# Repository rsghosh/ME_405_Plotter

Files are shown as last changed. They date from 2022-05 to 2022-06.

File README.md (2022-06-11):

# ME 405 Pen Plotter

Ryan Ghosh and Ryan Flaherty (mecha18)

ME 405-03

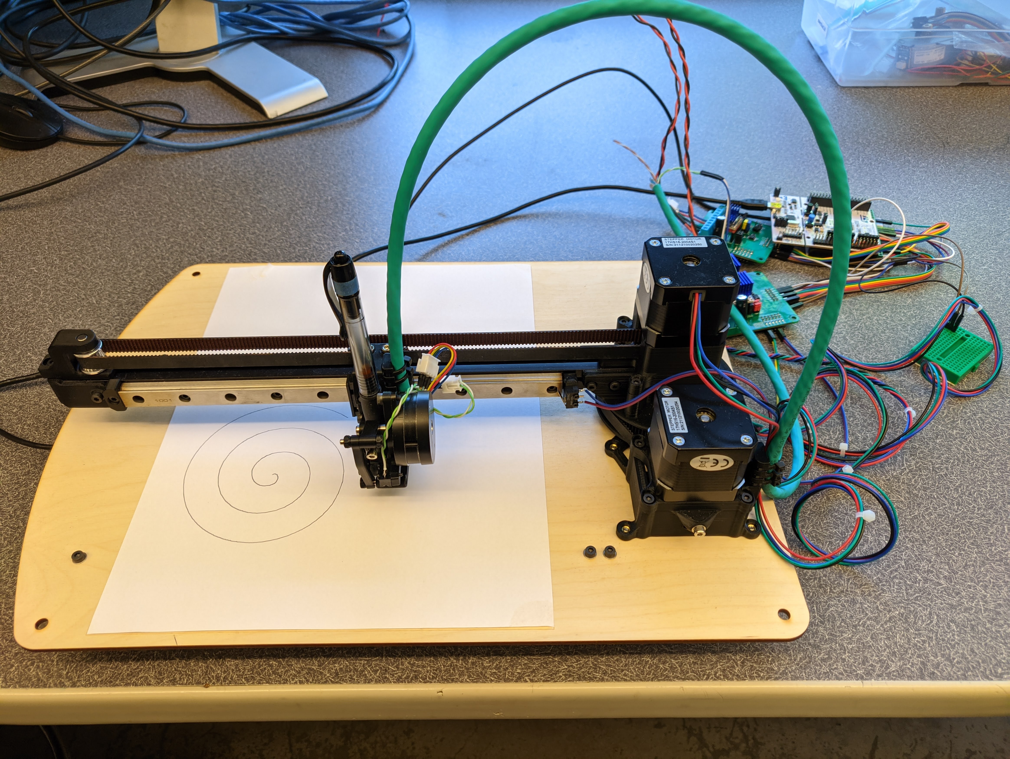
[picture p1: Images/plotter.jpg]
Pen Plotter


## Introduction

For our ME 405 term project, we designed, built, and programmed a polar pen plotter.
A Nucleo board on the plotter reads an hpgl file, converts the commands to motor positions, and controls the stepper drivers to make the plotter draw. Meanwhile, a PC receives the commands over UART to draw the same shapes on the screen in sync with the plotter.

The following videos show the plotter in action:
- [Drawing a pentagon, hexagon, and line](https://photos.app.goo.gl/KpNNWDwEAwex2bkJ8)
- [Drawing a spiral](https://photos.app.goo.gl/GEohXohUGA1frtkg9)

## Python Code

[Documentation](https://rsghosh.github.io/ME_405_Plotter/)

[Source code](https://github.com/rsghosh/ME_405_Plotter/tree/master/Python_Code)

## CAD Files

SolidWorks files for the pen plotter can be found [here.](https://github.com/rsghosh/ME_405_Plotter/tree/master/CAD)

## STL and DXF Files

All custom parts for the plotter are either 3D-printed or laser-cut.

### 3D-Printed Files

All stl files can be found in the [STLs folder.](https://github.com/rsghosh/ME_405_Plotter/tree/master/STLs)

In each filename, `_x#` indicates the quantity required, and `_rev#` indicates the revision number.

### Laser-Cut Files

The base for the plotter should be laser-cut from 3mm or 0.125" thick material. The dxf file can be found in the [DXFs folder.](https://github.com/rsghosh/ME_405_Plotter/tree/master/DXFs)

## Bill of Materials

The following table contains all the parts you need for the pen plotter that are not either 3D-printed or laser-cut:

| Item # | Description | Quantity | Source |
| --- | --- | --- | --- |
| 1 | 1515 Extrusion (300mm long) | 3 | [Amazon](https://www.amazon.com/MakerBeam-XL-Anodized-300x15x15mm-Pieces/dp/B06XJ5G5QY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)  |
| 2 | MGN12C Rail (240mm long) | 1 | [RobotDigg](https://www.robotdigg.com/product/766/Quality-440C-SUS-MGN12-linear-rail-with-carriage) |
| 3 | NEMA17 Stepper Motor | 2 | [Printed Solid](https://www.printedsolid.com/collections/motors/products/ldo-nema-17-motor-cooler-ldo-42sth40-1004asr)  |
| 4 | 2GT 20T Toothed Idler (for 9mm belt)  | 1 | [Printed Solid](https://www.printedsolid.com/products/gates-powergrip-2gt-toothed-idler-5mm-id?variant=21236971274325) |
| 5 | 2GT 20T Pulley (for 9mm belt) | 2 | [Printed Solid](https://www.printedsolid.com/products/gates-powergrip-2gt-pulley?variant=21236966948949)  |
| 7 | 6201 Bearing | 2 | [AliExpress](https://www.aliexpress.com/item/32861605867.html) |
| 8 | 5x25mm Shaft | 1 | [AliExpress](https://www.aliexpress.com/item/2255800484105446.html?gatewayAdapt=4itemAdapt) |
| 9 | 3x20mm Shaft | 3 | [Misumi](https://us.misumi-ec.com/vona2/detail/110300086920/?HissuCode=NSFR3-20)  |
| 10 | 5x7x0.5mm Shim | 2 | [AliExpress](http://s.click.aliexpress.com/e/_sq74Gk) |
| 11 | Omron D2F-L Microswitch | 3 | [Digikey](https://www.digikey.com/en/products/detail/omron-electronics-inc-emc-div/D2F-01L/83264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) |
| 12 | M3 Square Nut (DIN 562) | 36 | [McMaster-Carr](https://www.mcmaster.com/97259A101/)  |
| 13 | M3 x 8mm Socket Head Cap Screw | 59 | [McMaster-Carr](https://www.mcmaster.com/91290a113) |
| 14 | M3 x 10mm Socket Head Cap Screw | 5 | [McMaster-Carr](https://www.mcmaster.com/91290A115/)  |
| 15 | M3 x 12mm Socket Head Cap Screw | 12 | [McMaster-Carr](https://www.mcmaster.com/91290A117) |
| 16 | M3 x 20mm Socket Head Cap Screw | 2 | [McMaster-Carr](https://www.mcmaster.com/91290A123/)  |
| 17 | M3 Heat-Set Insert (M3 x D5.0 x L4.0) | 27 | [AliExpress](http://s.click.aliexpress.com/e/oMUr6YsC) |
| 18 | M3 Washer (narrow) | 8 | [McMaster-Carr](https://www.mcmaster.com/91166A210/)  |
| 19 | M3 Washer (large) | 4 | [McMaster-Carr](https://www.mcmaster.com/91100A120/)  |
| 20 | 36mm Round NEMA14 Stepper | 1 | [Printed Solid](https://www.printedsolid.com/products/ldo-nema14-36mm-round-pancake-motor-ldo-36sth17-1004ah)
| 21 | M5 x 45mm Socket Head Cap Screw | 1 | [McMaster-Carr](https://www.mcmaster.com/91290A260/)  |
| 22 | M2 x 12mm Pan Head Self Tapping Screw | 6 | [AliExpress](http://s.click.aliexpress.com/e/ojcLGreY) |
| 23 | M5 Locknut | 1 | [McMaster-Carr](https://www.mcmaster.com/90576A104/)  |
| 24 | Unthreaded Bumper | 4 | [McMaster-Carr](https://www.mcmaster.com/9540K921/) |
| 25 | Nucleo-L476RG | 1 | [Digikey](https://www.digikey.com/en/products/detail/stmicroelectronics/NUCLEO-L476RG/5347711) |
| 26 | TMC2208 Stepstick | 3 | [Amazon](https://www.amazon.com/Printer-TMC2208-Screwdriver-Controller-Ramps1-4/dp/B082LSQWZF) |
| 27 | Stepper Driver Board | 2 | |

## Wiring

### Stepper Driver Board #1
| Signal | Nucleo Pin | Color |
| --- | --- | --- |
| EN1 | C2 | red |
| EN2 | C3 | green |
| GND | GND | black |
| 3V3 | 3V3 | gray  |
| CLK | PB6 | brown |
| CS1 | PB8 | yellow|
| CS2 | PB9 | orange|
| SCK | PB13 (SPI2_SCLK)  | blue  |
| MOSI | PB15 (SPI2_MOSI)  | white |
| MISO | PB14 (SPI2_MISO)  | purple|

### Stepper Driver Board #2
| Signal | Nucleo Pin | Color |
| --- | --- | --- |
| EN1 | C6 | blue  |
| GND | GND | green |
| 3V3 | 3V3 | yellow|
| CLK | PB6 | brown |
| CS1 | C7 | orange|
| CS2 | 3V3 | white |
| SCK | PB13 (SPI2_SCLK)  | blue  |
| MOSI | PB15 (SPI2_MOSI)  | white |
| MISO | PB14 (SPI2_MISO)  | purple|

### Limit Switch Wiring

The wires should be soldered to the outermost legs on the limit switches so that they are normally closed.

| Endstop | Stepper Board # | Pin |
| --- | --- | --- |
| theta | 1 | REFL1 |
| radius | 1 | REFL2 |
| pen up/down | 2 | REFL1 |

### Stepper Driver Board Jumpers

To set the TMC2208 drivers to use 8 microsteps, jumpers should be placed on the JP6 and JP7 headers to short MS1 and MS2 to GND.

### Setting VREF

To calculate the VREF values to set on the TMC2208 drivers, the desired RMS current should be multiplied by 1.41 ohm.

The following table shows the VREF values we used:

| Motor | Target RMS Current (A) | VREF (V)  |
| --- | --- | --- |
| theta | 1.13 | 1.59 |
| radius | 1.13 | 1.59 |
| pen up/down | 0.35 | 0.49 |

### Wiring Example

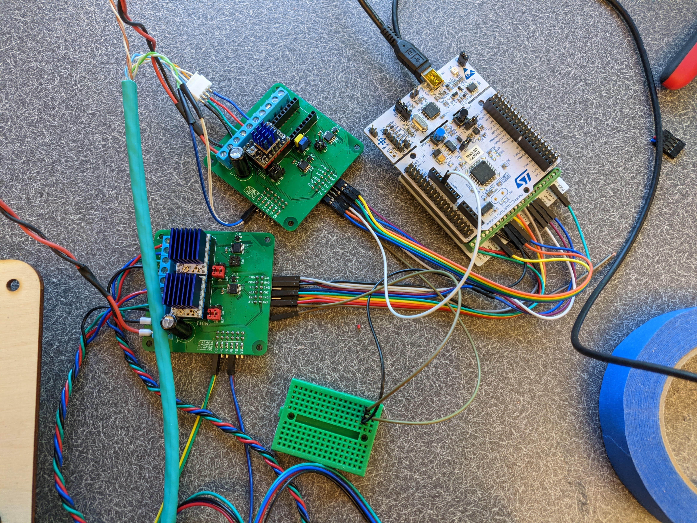
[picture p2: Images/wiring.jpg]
Wiring Example


## Task Diagram

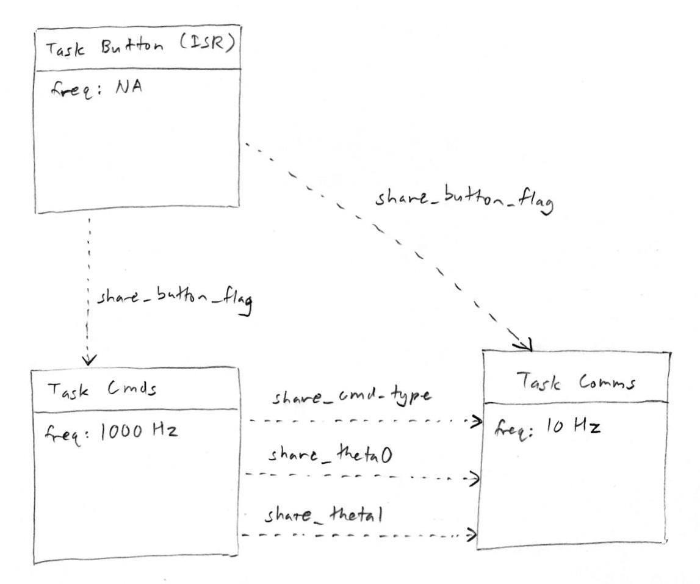
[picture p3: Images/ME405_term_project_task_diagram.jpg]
Task Diagram


## Kinematics

Since our pen plotter uses one motor for controlling the angle of the arm and another to control the radius, we had to use inverse kinematics to determine the motor angles needed to get the pen to the target x and y coordinates. We used the Newtom-Raphson algorithm to find the required motor angles to reach the target position. The following images show the steps we took to find the matrices and equations we would use in the algorithm:

1. Simplified schematic of the robot with links and pivots
2. Forward kinematics: determine `x = f(theta)`, where theta is the motor angles and x is the pen position
3. Find the Jacobian matrix for the system
4. Differentiate `x = f(theta)` with respect to time to find velocity
5. Find g(theta), where `g(theta) = x - f(theta)` and x is a constant target position. Then differentiate g with respect to theta.

We then used these equations in the NewtonRaphson function in [tasks.py](https://github.com/rsghosh/ME_405_Plotter/blob/master/Python_Code/tasks.py) to convert pen positions read from the hpgl file into motor angles.

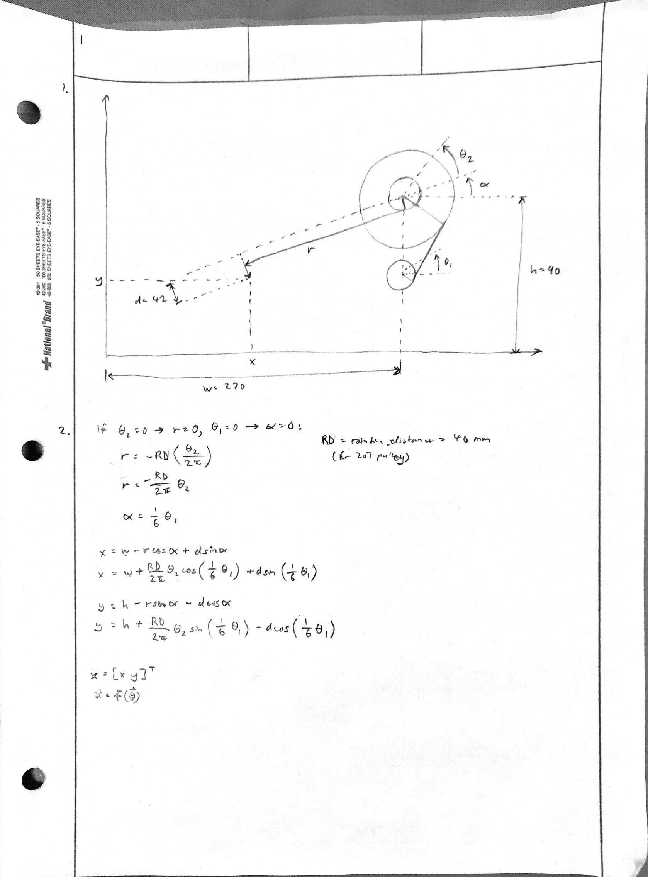
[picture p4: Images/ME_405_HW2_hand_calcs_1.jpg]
Kinematics steps 1-2


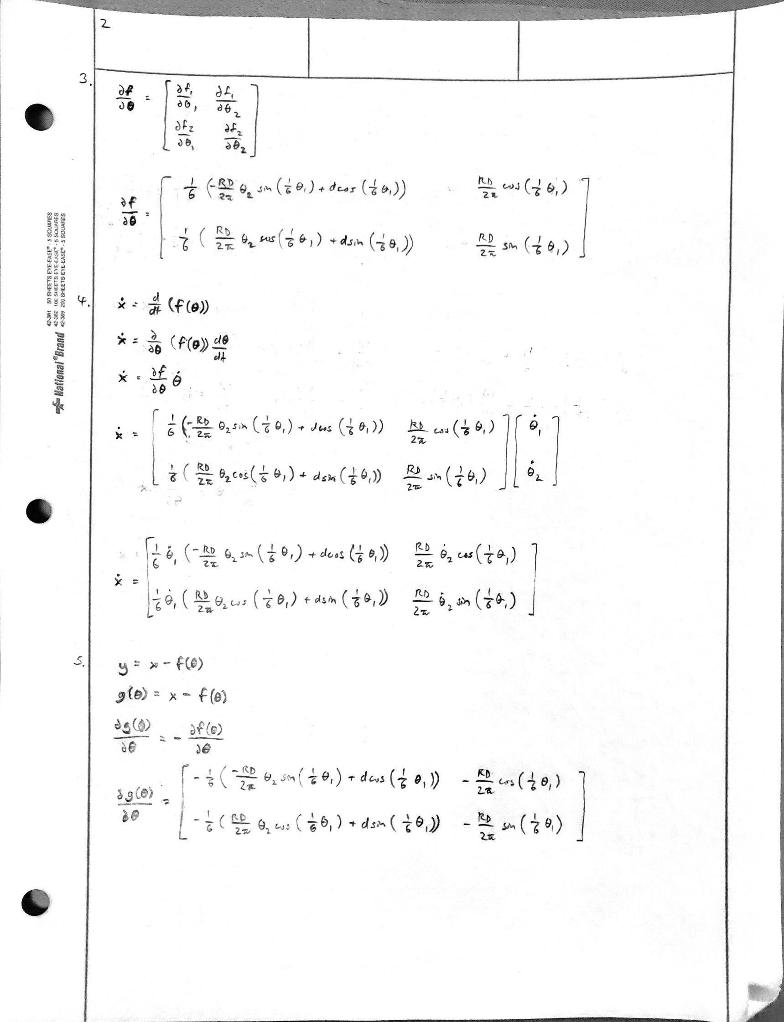
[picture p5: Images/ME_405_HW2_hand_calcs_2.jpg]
Kinematics steps 3-5


## Program Flow

[tasks.py](https://github.com/rsghosh/ME_405_Plotter/blob/master/Python_Code/tasks.py) contains the main function that runs on the Nucleo. The program proceeds in the following steps:
- Read an hpgl file and split it into separate commands
- convert target positions into millimeters
- Interpolate between points so that the minimum distnance between any two points is less than or equal to `MAX_MM_DIST` (which we set to 0.5mm)
- Use Newton-Raphson to convert the positions to theta angles for the motors
- Convert theta angles to numbers in units of microsteps that can be sent to the TMC4210s as the X_TARGET
- Configure the TMC4210 and TMC2208 chips
- Home all three steppers
- Wait for a button press
- Start the two tasks:
  - task_cmds: reads through the commands and sends them to the TMC4210s
  - task_comms: sends the current command to the PC via UART to be plotted on the screen
- Disable the motors once the end of the command list has been reached

More details on the individual functions can be found in the [documentation for the python files.](https://rsghosh.github.io/ME_405_Plotter/)

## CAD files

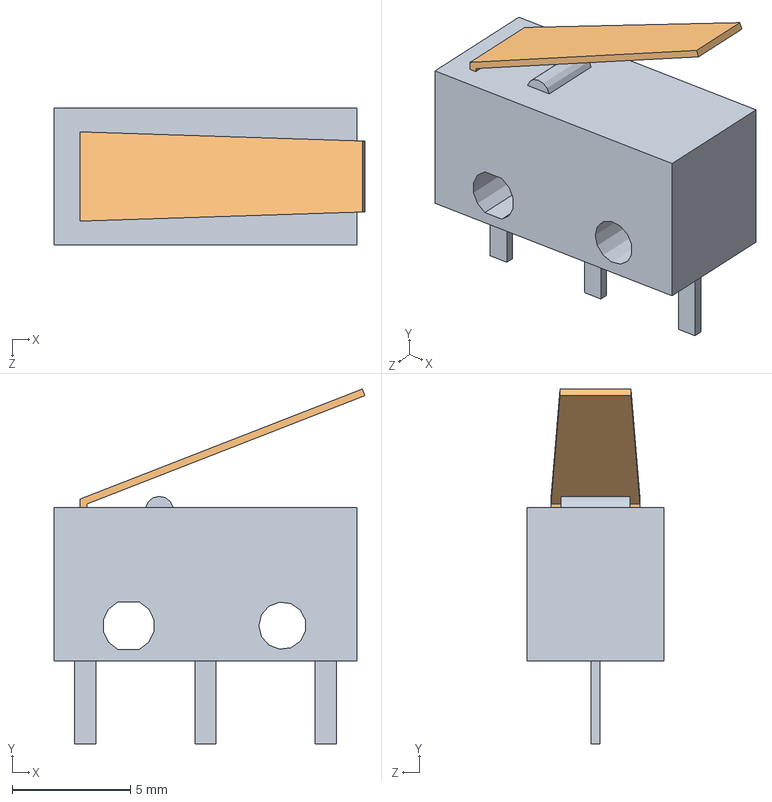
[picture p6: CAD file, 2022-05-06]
CAD/hardware/D2F_01L_Solidworks/D2F_01L.SLDASM
13.1 x 15.0 x 5.80 mm
D2F_01L_BASE
D2F_01L_ACTUATOR

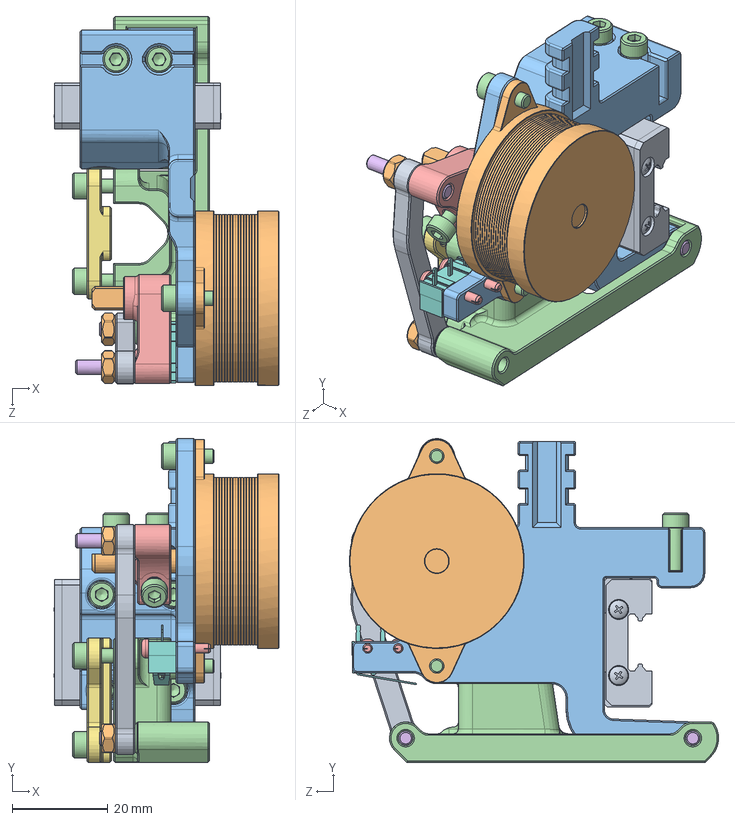
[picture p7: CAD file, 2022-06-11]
CAD/Toolhead.SLDASM
46.9 x 67.7 x 77.1 mm
MGN12C, LINEAR GUIDE BLOCK
LDO-36STH20-1004AH Mockup
Carriage^Toolhead
Pen Arm^Toolhead
Motor Arm^Toolhead
Shaft 3x20 x 3
Pen Clamp^Toolhead
49 MICRO D2F-L
Link^Toolhead
3mm Shaft Retainer x 2
square nut thin grade b_din
socket head cap screw_am x 13
pan head tapping screw_am x 2
94180A331_HEAT-SET INSERTS FOR PLASTICS x 4

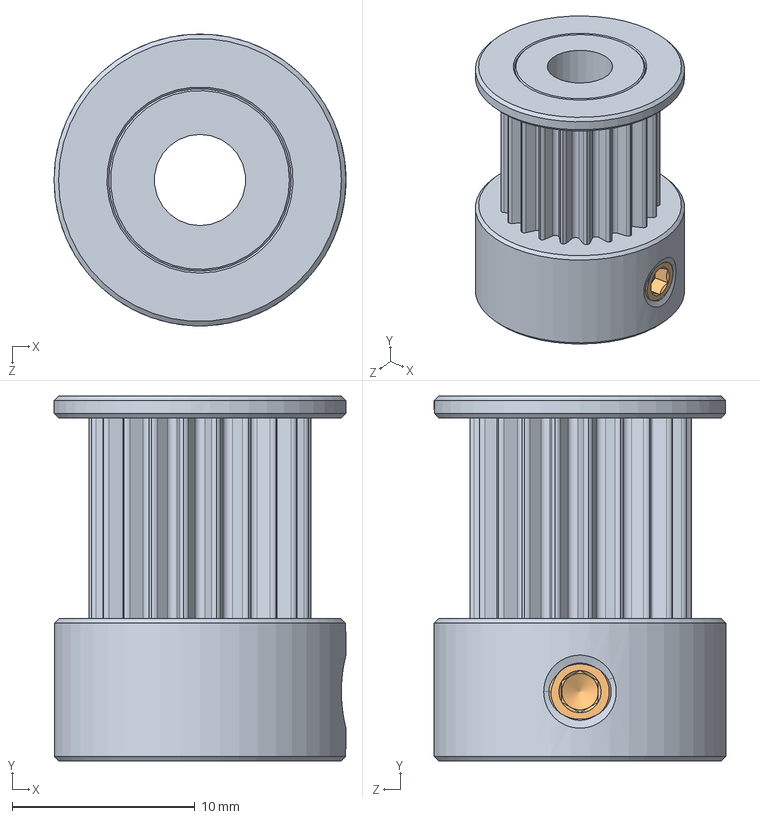
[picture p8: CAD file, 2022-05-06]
CAD/hardware/Pulley 9mm 20T 2GT/Pulley, 9mm GT2.SLDASM
16.0 x 20.0 x 16.0 mm
Pulley, 9mm GT2
91390A110

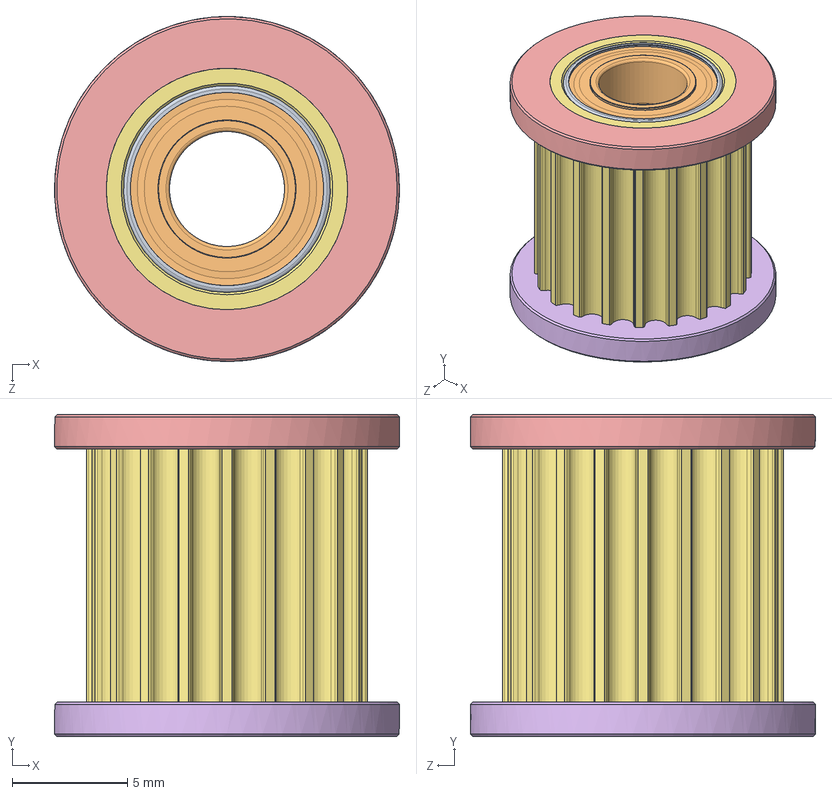
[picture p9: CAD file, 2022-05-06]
CAD/hardware/20T Toothed Idler/Pulley, 2GT 20T Toothed Idler (11mm wide).SLDASM
15.0 x 14.0 x 15.0 mm
Pulley, 2GT 20T Toothed Idler (11mm wide)_4
Pulley, 2GT 20T Toothed Idler (11mm wide)_14
Pulley, 2GT 20T Toothed Idler (11mm wide)_8
Pulley, 2GT 20T Toothed Idler (11mm wide)_19
Pulley, 2GT 20T Toothed Idler (11mm wide)_17
Pulley, 2GT 20T Toothed Idler (11mm wide)_16
Pulley, 2GT 20T Toothed Idler (11mm wide)_13
Pulley, 2GT 20T Toothed Idler (11mm wide)_22
Pulley, 2GT 20T Toothed Idler (11mm wide)_18
Pulley, 2GT 20T Toothed Idler (11mm wide)
Pulley, 2GT 20T Toothed Idler (11mm wide)_9
Pulley, 2GT 20T Toothed Idler (11mm wide)_2
Pulley, 2GT 20T Toothed Idler (11mm wide)_10
Pulley, 2GT 20T Toothed Idler (11mm wide)_23
Pulley, 2GT 20T Toothed Idler (11mm wide)_20
Pulley, 2GT 20T Toothed Idler (11mm wide)_3
Pulley, 2GT 20T Toothed Idler (11mm wide)_5
Pulley, 2GT 20T Toothed Idler (11mm wide)_11
Pulley, 2GT 20T Toothed Idler (11mm wide)_21
Pulley, 2GT 20T Toothed Idler (11mm wide)_12
Pulley, 2GT 20T Toothed Idler (11mm wide)_6
Pulley, 2GT 20T Toothed Idler (11mm wide)_15
Pulley, 2GT 20T Toothed Idler (11mm wide)_7

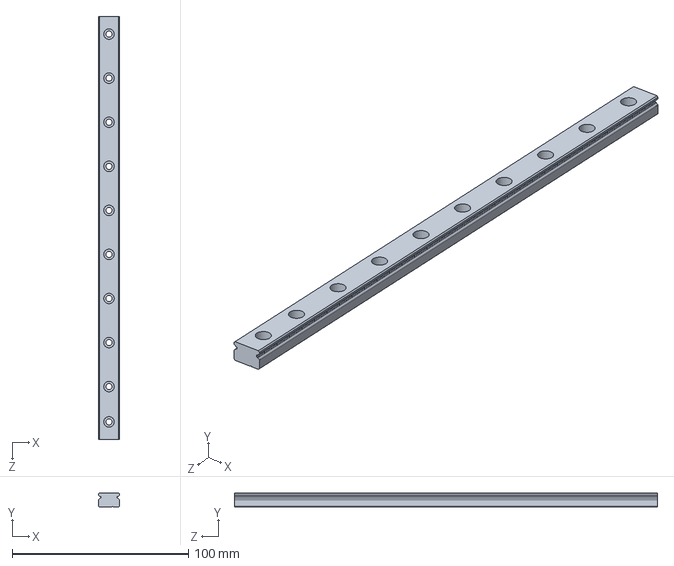
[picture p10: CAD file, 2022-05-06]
CAD/hardware/MGN12C Linear Guide/MGN12 LINEAR GUIDE RAIL, CONFIGURABLE.SLDPRT
12.0 x 8.00 x 240.0 mm

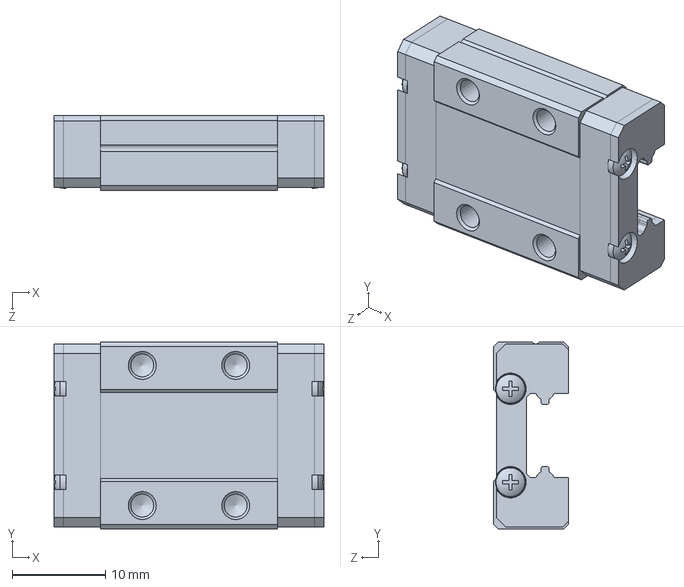
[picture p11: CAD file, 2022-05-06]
CAD/hardware/MGN9CZFC [Hiwin].SLDPRT
28.9 x 20.0 x 8.00 mm

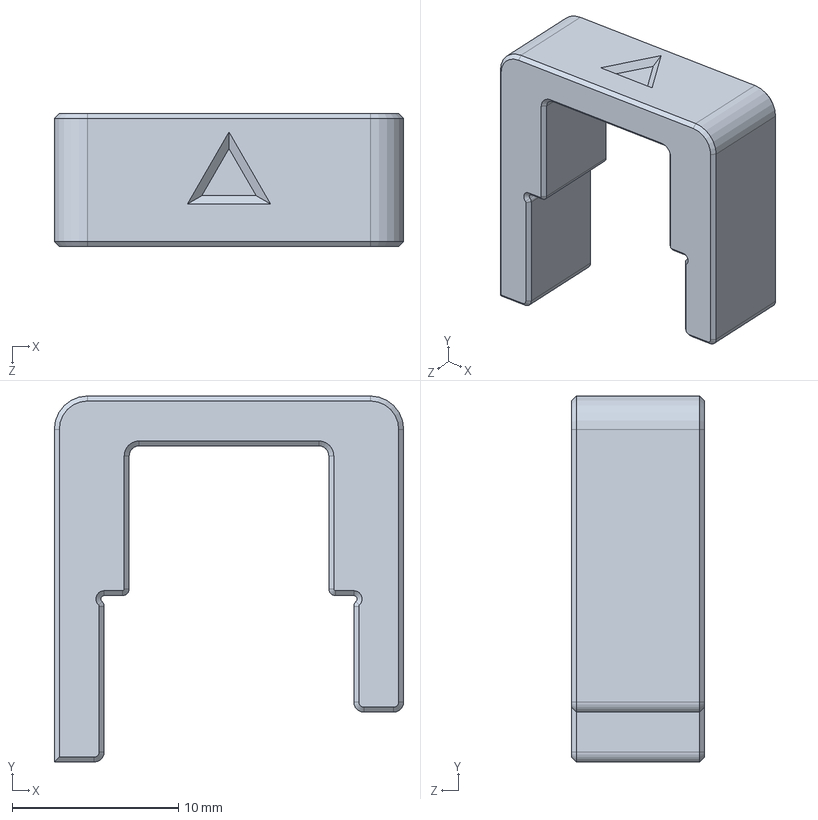
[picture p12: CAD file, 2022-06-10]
CAD/tools/MGN12 1515 Rail Installation Guide.SLDPRT
21.0 x 22.0 x 8.00 mm

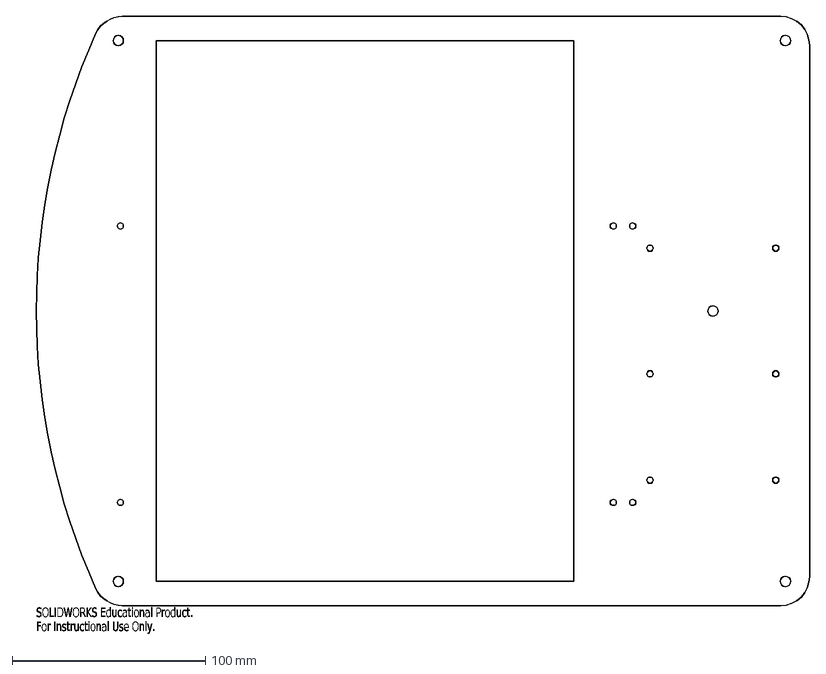
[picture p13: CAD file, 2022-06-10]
DXFs/BASE-PLATE-2.DXF
SOLIDWORKS Educational Product.
For Instructional Use Only.

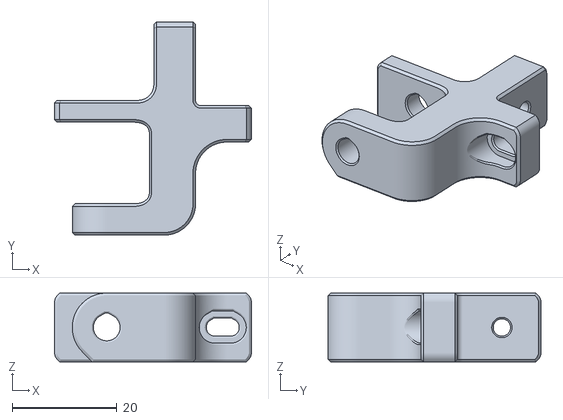
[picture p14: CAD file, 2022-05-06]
STLs/Arm/idler_tensioner_moving_x1_rev1.STL
37.7 x 40.8 x 13.2

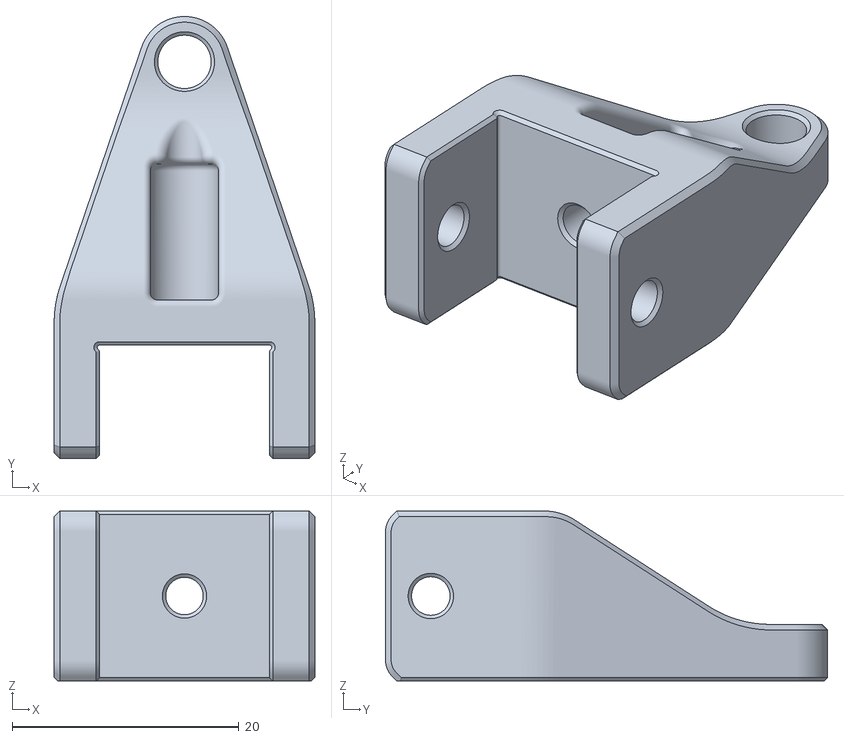
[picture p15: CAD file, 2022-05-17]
STLs/Base/plate_mount_x2_rev1.STL
23.0 x 39.0 x 15.0

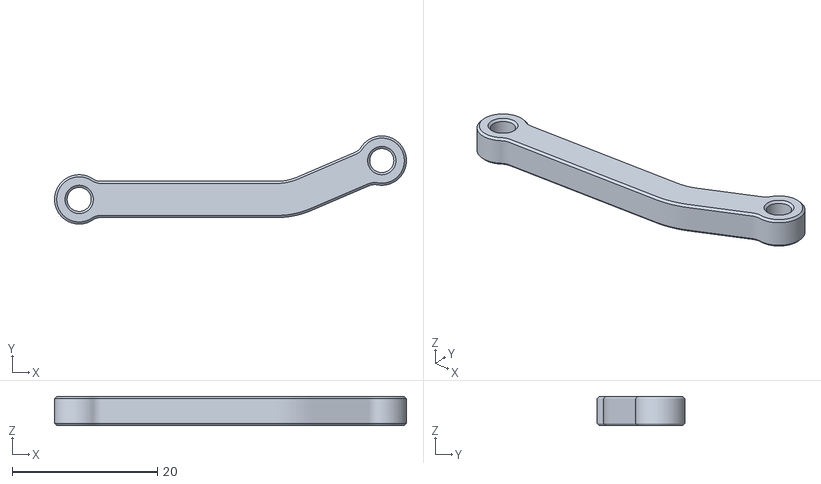
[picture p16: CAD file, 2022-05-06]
STLs/Toolhead/link_x1_rev1.STL
48.4 x 12.1 x 4.00

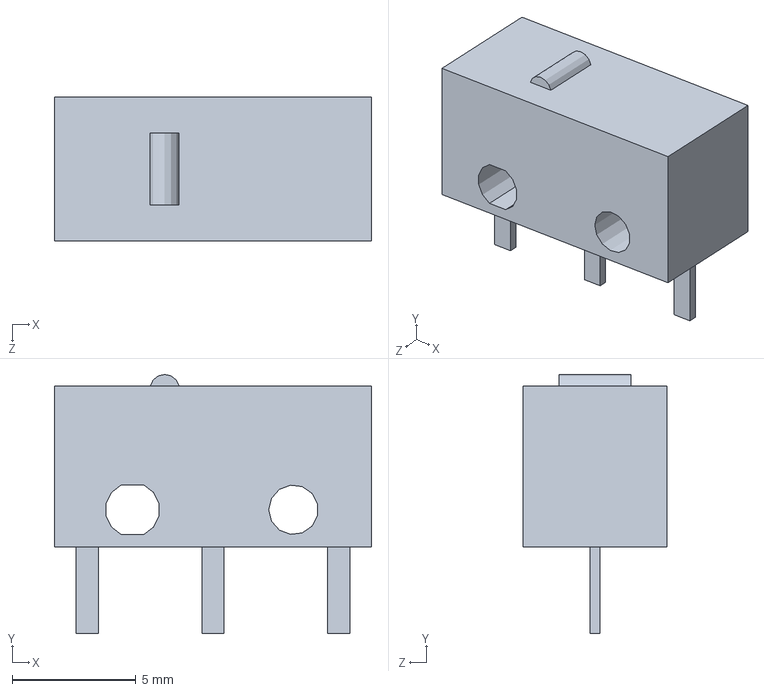
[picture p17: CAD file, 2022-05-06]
CAD/hardware/D2F_01L_Solidworks/D2F_01L_BASE.SLDPRT
12.8 x 10.5 x 5.80 mm

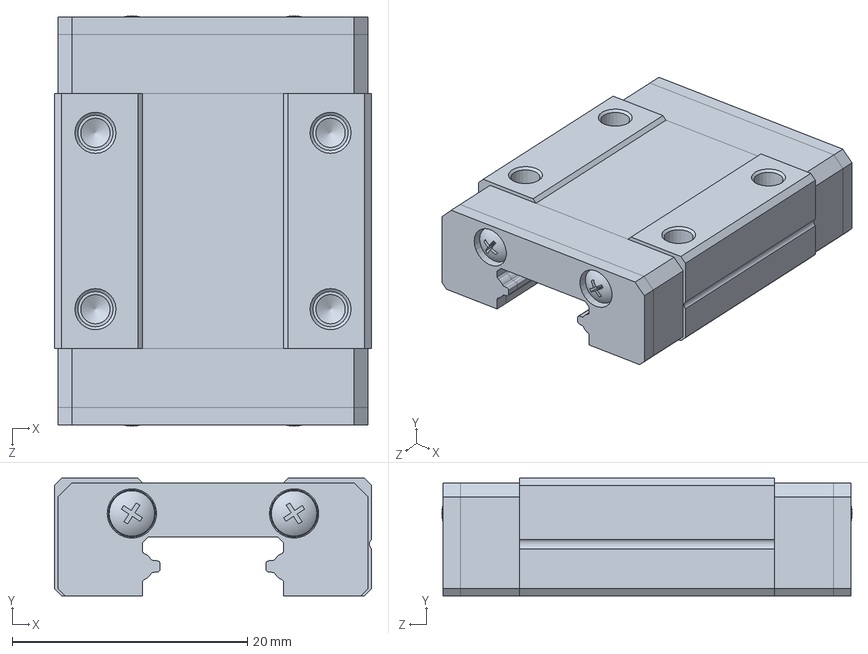
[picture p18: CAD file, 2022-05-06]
CAD/hardware/MGN12C Linear Guide/MGN12C, LINEAR GUIDE BLOCK.SLDPRT
27.0 x 10.0 x 34.9 mm

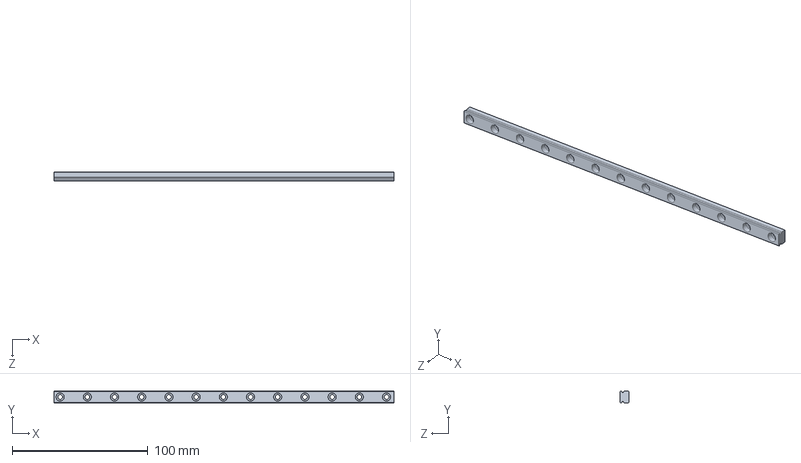
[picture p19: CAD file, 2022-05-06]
CAD/hardware/MGN9 Rail 250mm.SLDPRT
250.0 x 9.00 x 6.50 mm

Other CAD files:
CAD/hardware/20T Toothed Idler/Pulley, 2GT 20T Toothed Idler (11mm wide)_22.SLDPRT
CAD/hardware/20T Toothed Idler/Pulley, 2GT 20T Toothed Idler (11mm wide)_5.SLDPRT
CAD/MDF Base Plate (Laser Cut).SLDPRT
STLs/Arm/radius_limit_switch_mount_x1_rev1.STL
CAD/3mm Shaft Retainer.SLDPRT
CAD/Clipboard Clamp.SLDPRT
CAD/Printed M5 Washer.SLDPRT
CAD/hardware/20T Toothed Idler/Pulley, 2GT 20T Toothed Idler (11mm wide).SLDPRT
CAD/hardware/20T Toothed Idler/Pulley, 2GT 20T Toothed Idler (11mm wide)_10.SLDPRT
CAD/hardware/20T Toothed Idler/Pulley, 2GT 20T Toothed Idler (11mm wide)_11.SLDPRT
CAD/hardware/20T Toothed Idler/Pulley, 2GT 20T Toothed Idler (11mm wide)_12.SLDPRT
CAD/hardware/20T Toothed Idler/Pulley, 2GT 20T Toothed Idler (11mm wide)_13.SLDPRT
CAD/hardware/20T Toothed Idler/Pulley, 2GT 20T Toothed Idler (11mm wide)_14.SLDPRT
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

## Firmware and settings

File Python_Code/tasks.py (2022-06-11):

'''@file        tasks.py
   @brief       This file contains the main function for controlling the plotter,
                along with task functions for sending position commands to the
                stepper drivers and to a PC via UART.
   @author      Ryan Ghosh
   @copyright   This file is licensed under the CC BY-NC-SA 4.0
                Please visit https://creativecommons.org/licenses/by-nc-sa/4.0/
                for terms and conditions of the license.
   @date        June 10, 2022
'''

import pyb
import math
from ulab import numpy as np
import array
import time
from stepper_driver import Stepper_Driver
import gc
import cotask
import task_share

# constants for the vector file and converting it
FILENAME = 'drawing.hpgl'
DPI = 1016
MM_PER_IN = 25.4
MAX_MM_DIST = 0.5

# constants for converting coordinates to theta
W = 270
H = 90
D = 42
RD = 40

# TMC4210 and TMC2208 settings
STEPS_PER_ROTATION  = 200
MICROSTEPS          = 8
F_CLK               = 20000000
PULSE_DIV           = 5
RAMP_DIV            = 5

# constants for converting theta to microsteps
MS_PER_RADIAN = 1 / (2 * math.pi) * STEPS_PER_ROTATION * MICROSTEPS

# constants for converting microsteps to account for homing angle and motor direction
STEPS_PER_ROTATION  = 200
MOTOR1_HOMING_ANGLE = -int(68.27 / 360 * STEPS_PER_ROTATION * MICROSTEPS * 6)
MOTOR1_POLARITY     = 1
MOTOR2_HOMING_ANGLE = -int((34.7/2 + 60.24 + 0.9) / 40 * STEPS_PER_ROTATION * MICROSTEPS)
MOTOR2_POLARITY     = -1

# pen positions
PEN_DOWN_DEG = 65.5
PEN_DOWN_MS = int(PEN_DOWN_DEG / 360 * STEPS_PER_ROTATION * MICROSTEPS)
PEN_UP_DEG = 40
PEN_UP_MS = int(PEN_UP_DEG / 360 * STEPS_PER_ROTATION * MICROSTEPS)

# speed settings in rad/s
MOTOR1_SPEED        = 15
MOTOR1_HOMING_SPEED = 3
MOTOR2_SPEED        = 15 
MOTOR2_HOMING_SPEED = 6
MOTOR3_SPEED        = 15
MOTOR3_HOMING_SPEED = 6

# other motor settings
MOTOR1_X_MAX = 20000
MOTOR2_X_MAX = 20000
MOTOR3_X_MAX = 20000
MOTOR1_V_MIN = 10
MOTOR2_V_MIN = 10
MOTOR3_V_MIN = 1
MOTOR1_A_MAX = 80
MOTOR2_A_MAX = 80
MOTOR3_A_MAX = 60

# cmd_type constants
TYPE_PEN_UP     = 1
TYPE_PEN_DOWN   = 2
TYPE_CMDS_DONE  = 3
TYPE_COMMS_DONE = 4

# global variables
## Button flag
share_button_flag = None

## List of stepper commands, in units of microsteps
cmd_list = None

## Stepper_Driver objects for controlling the 3 steppers
drivers = [3]

# button interrupt function
def onButtonPressFCN(IRQ_src):
    ''' @brief          Sets the button flag when the button is pressed.
        @details        An interrupt function triggered when the blue button
                        on the Nucleo is pressed. This function sets the
                        button_flag share to 1 to indicate the button has been pressed.
        @param IRQ_src  Reference to the hardware device that caused the interrupt to occur.
    '''

    global share_button_flag
    share_button_flag.put(1)

## Button interrupt
button_int = pyb.ExtInt(pyb.Pin.cpu.C13, pyb.ExtInt.IRQ_FALLING, 
                        pyb.Pin.PULL_NONE, callback=onButtonPressFCN)

# functions for driving steppers
def get_velocity_setting(rad_per_sec):
    ''' @brief              Converts the velocity value that is passed in.
        @details            Takes in a velocity value in rad/s and converts it to
                            a corresponding value to be used in the V_MIN or V_MAX
                            register of a TMC4210.
        @param rad_per_sec  Velocity value in rad/s.
        @return             Corresponding velocity value to be used in the TMC4210 registers.
    '''

    # see p.31 of TMC4210 datasheet
    R = rad_per_sec / (2 * math.pi) * STEPS_PER_ROTATION * MICROSTEPS   # microstep frequency (Hz)
    return int(R * 2**PULSE_DIV * 2048 * 32 / F_CLK)

def get_acceleration_setting(rad_per_sec2):
    ''' @brief                  Converts the acceleration value that is passed in.
        @details                Takes in an acceleration value in rad/s^2 and converts it
                                to a corresponding value to be used in the A_MAX
                                register of a TMC4210.
        @param rad_per_sec2     Acceleration value in rad/s^2.
        @return                 Corresponding acceleration value to be used in the TMC4210 registers.
    '''

    # see p.31-32 of TMC4210 datasheet
    delta_R = rad_per_sec2 / (2 * math.pi) * STEPS_PER_ROTATION * MICROSTEPS    # microstep frequency (Hz/s)
    return int(delta_R * 2**(PULSE_DIV + RAMP_DIV + 29) / (F_CLK * F_CLK))

def get_pmul_and_pdiv_setting(a_max):
    ''' @brief          Finds values for PMUL and PDIV.
        @details        Finds suitable values for PMUL and PDIV to match the
                        A_MAX value that is passed in, along with the existing
                        RAMP_DIV and PULSE_DIV settings.
        @param a_max    A_MAX value to match with.
        @return         A tuple containing PMUL, PDIV values.
    '''

    # see p.26 of TMC4210 datasheet
    pm =-1
    pd = -1
    p = a_max / (128.0 + 2**(RAMP_DIV - PULSE_DIV))
    p_reduced = p * 0.99

    for pdiv in range(14):
        pmul = int(p_reduced * 8.0 * 2**pdiv) - 128
        if (0 <= pmul) and (pmul <= 127):
            pm = pmul + 128
            pd = pdiv
    
    return pm, pd

def convert_motor1_target(microsteps):
    ''' @brief              Converts a motor1 target value to send to the TMC4210.
        @details            Takes in a target value for motor1 in units of microsteps
                            And converts it to a corresponding value to send to the
                            TMC4210, based on the direction of the motor and its angle
                            when the limit switch is triggered.
        @param microsteps   Target position in microsteps.
        @return             Target position for motor1 that can be sent to the TMC4210.
    '''

    # convert target position in microsteps to a position to send to the TMC4210
    return MOTOR1_POLARITY * (microsteps - MOTOR1_HOMING_ANGLE)

def convert_motor2_target(microsteps):
    ''' @brief              Converts a motor2 target value to send to the TMC4210.
        @details            Takes in a target value for motor2 in units of microsteps
                            And converts it to a corresponding value to send to the
                            TMC4210, based on the direction of the motor and its angle
                            when the limit switch is triggered.
        @param microsteps   Target position in microsteps.
        @return             Target position for motor2 that can be sent to the TMC4210.
    '''

    # convert target position in microsteps to a position to send to the TMC4210
    return MOTOR2_POLARITY * (microsteps - MOTOR2_HOMING_ANGLE)

# motion planning/coordinate conversion functions
def g(x, theta):
    ''' @brief          g(x, theta) function for use in the Newton-Raphson algorithm.
        @details        A function of x and theta that should be driven to 0 to
                        iteratively find the value of theta that satisfies x = f(theta),
                        where x is the desired pen position and theta is the motor positions.
        @param x        tuple of (x_target, y_target).
        @param theta    tuple of (theta0, theta1).
        @return         g(theta) for the theta guess that is passed in.
    '''

    return [x[0] - (W + RD/(2*math.pi)*theta[1]*math.cos(1/6*theta[0]) + D*math.sin(1/6*theta[0])),
            x[1] - (H + RD/(2*math.pi)*theta[1]*math.sin(1/6*theta[0]) - D*math.cos(1/6*theta[0]))]

def dg_dtheta(theta):
    ''' @brief          dg/dtheta(theta) function for use in the Newton-Raphson algorithm.
        @details        A function of theta that is used to iteratively find the
                        value of theta that satisfies x = f(theta),
                        where x is the desired pen position and theta is the motor positions.
        @param theta    tuple of (theta0, theta1).
        @return         dg(theta)/dtheta for the theta guess that is passed in.
    '''

    return np.array([[-1/6*(-RD/(2*math.pi)*theta[1]*math.sin(1/6*theta[0]) + D*math.cos(1/6*theta[0])), -RD/(2*math.pi)*math.cos(1/6*theta[0])],
                     [-1/6*(RD/(2*math.pi)*theta[1]*math.cos(1/6*theta[0]) + D*math.sin(1/6*theta[0])), -RD/(2*math.pi)*math.sin(1/6*theta[0])]])

def NewtonRaphson(fcn, jacobian, guess, thresh):
    ''' @brief              Iteratively solves the roots of y = g(theta).
        @details            Iteratively finds values for theta to drive the passed
                            in fcn to within thresh of 0.
        @param fcn          The function to find the roots of.
        @param jacobian     Jacobian matrix for the system
        @param guess        Initial guess for theta.
        @param thresh       Allowable error when driving fcn to 0.
        @return             Resulting theta roots.
    '''

    theta = guess
    g = fcn(theta)
    while abs(g[0]) > thresh or abs(g[1]) > thresh:
        theta_arr = (np.asarray(theta)).transpose()
        g_arr = (np.asarray(g)).transpose()
        theta_arr = theta_arr - np.dot(np.linalg.inv(jacobian(theta)), g_arr)
        theta = np.ndarray.tolist((theta_arr).transpose())
        g = fcn(theta)
    return theta

def create_cmd_list():
    ''' @brief          Creates a list of motor commands from an hpgl file.
        @details        Converts each command in an hpgl file to a tuple
                        containing the type ("PU" or "PD" for "pen up" or "pen down"),
                        an array of theta0 values to send to the driver1 TMC4210, and
                        an array of theta1 values to send to the driver2 TMC4210.
        @return         A list of command tuples.
    '''

    # read hpgl file
    with open(FILENAME, 'r') as file:
        line = file.readlines()[0]

    # split into commands
    cmd_str_list = line.split(';')

    # remove commands other than PU and PD
    i = 0
    while i < len(cmd_str_list):
        if 'PU' in cmd_str_list[i] or 'PD' in cmd_str_list[i]:
            i += 1
        else:
            cmd_str_list.remove(cmd_str_list[i])

    # split each command into type and coordinates, and convert to mm
    # each element in cmd_list is a tuple with 3 items:
    #   type (str)
    #   x_arr (array.array of floats)
    #   y_arr (array.array of floats)
    cmd_list = []
    for cmd in cmd_str_list:
        type = cmd[0:2]             # str (either PU or PD)
        args = cmd[2:]              # str containing all args
        # if the command has arguments:
        if len(args):
            arg_list = args.split(',')  # str list of arguments

            # spit args into lists of floats
            x_arr = array.array('f')
            y_arr = array.array('f')
            i = 0
            while i < len(arg_list):
                x_arr.append(float(arg_list[i]) / DPI * MM_PER_IN)
                y_arr.append(float(arg_list[i + 1]) / DPI * MM_PER_IN)
                i += 2
            
            # tuple containing type, x coordinates, y coordinates
            cmd_list.append((type, x_arr, y_arr))

    # interpolate and add more points so the max movement distance
    # in any axis is MAX_MM_DIST
    prev_x = None
    prev_y = None
    for cmd_idx in range(len(cmd_list)):
        type = cmd_list[cmd_idx][0]
        x_arr = cmd_list[cmd_idx][1]
        y_arr = cmd_list[cmd_idx][2]
        new_x_arr = array.array('f')
        new_y_arr = array.array('f')
        if prev_x is None:
            prev_x = x_arr[0]
            prev_y = y_arr[0]
            i = 1
        else:
            i = 0
        while i < len(x_arr):
            x_diff = x_arr[i] - prev_x
            y_diff = y_arr[i] - prev_y
            
            # increments - 1 is the number of coordinate pairs that need to be added
            increments = int(math.ceil(max(abs(x_diff), abs(y_diff)) / MAX_MM_DIST))
            for p in range(increments - 1):
                x = prev_x + float(p + 1) / increments * x_diff
                y = prev_y + float(p + 1) / increments * y_diff
                new_x_arr.append(x)
                new_y_arr.append(y)
            new_x_arr.append(x_arr[i])
            new_y_arr.append(y_arr[i])
            prev_x = x_arr[i]
            prev_y = y_arr[i]
            i += 1
        cmd_list[cmd_idx] = (type, new_x_arr, new_y_arr)
    
    # convert to theta angles, then to microsteps, then convert to input for TMC4210
    # theta_guess = [1, -14]
    theta_guess = [2, -10]
    for cmd in cmd_list:
        x_arr = cmd[1]
        y_arr = cmd[2]
        for i in range(len(x_arr)):
            coord_pair = (x_arr[i], y_arr[i])
            theta = NewtonRaphson(lambda theta: g(coord_pair, theta),
                                  dg_dtheta, theta_guess, 1e-4)
            # debugging
            # print("theta %d done" % (i))

            x_arr[i] = convert_motor1_target(int(theta[0] * MS_PER_RADIAN))
            y_arr[i] = convert_motor2_target(int(theta[1] * MS_PER_RADIAN))
            
            theta_guess = theta

    return cmd_list

# for debugging:
def print_cmd_list(cmd_list):
    ''' @brief      Prints out the passed in cmd_list.
        @details    Prints out each command type ("PU" or "PD")
                    with the corrsponding coordinate list below it.
    '''

    for cmd in cmd_list:
        print(cmd[0])
        for i in range(len(cmd[1])):
            print('\t%f, %f' % (cmd[1][i], cmd[2][i]))

# task functions
def task_cmds_fun():
    ''' @brief      Task function for sending commands to the TMC4210s.
        @details    Generator function that waits for a button press to
                    begin, then reads through cmd_list and sets the
                    targets for each stepper driver. The function waits
                    for the current targets to be reached before sending
                    the next ones.
    '''

    global cmd_list
    global drivers

    # wait for button press
    while share_button_flag.get() != 1:
        yield 0

    # execute each command in cmd_list
    for cmd in cmd_list:

        # pen up or pen down
        if cmd[0] == "PU":
            driver3_target = PEN_UP_MS
            drivers[2].set_target(driver3_target)
            share_cmd_type.put(TYPE_PEN_UP)
        else:
            driver3_target = PEN_DOWN_MS
            drivers[2].set_target(driver3_target)
            share_cmd_type.put(TYPE_PEN_DOWN)
        yield 0

        # wait for driver3 (pen motor) to reach position
        while not drivers[2].target_reached(driver3_target):
            yield 0
        
        theta0_arr = cmd[1]
        theta1_arr = cmd[2]
        
        # for each coordinate pair in the command:
        for i in range(len(theta0_arr)):
            driver1_target = int(theta0_arr[i])
            driver2_target = int(theta1_arr[i])
            
            # set target positions
            drivers[0].set_target(driver1_target)
            drivers[1].set_target(driver2_target)
            share_theta0.put(driver1_target)
            share_theta1.put(driver2_target)
            yield 0
            
            # wait for driver1 to reach position
            while not drivers[0].target_reached(driver1_target):
                yield 0

            # wait for driver2 to reach position
            while not drivers[1].target_reached(driver2_target):
                yield 0

    # indicate the end of cmd_list has been reached
    share_cmd_type.put(TYPE_CMDS_DONE)
    yield 0
        
def task_comms_fun():
    ''' @brief      Task function for sending current commands to the PC.
        @details    Generator function that waits for a button press to
                    begin, then sends the current commands to the PC for
                    live plotting in sync with the physical plotter.
    '''

    # create UART object
    uart = pyb.UART(2)
    uart.init(115200, bits=8, parity=0, stop=1)

    # wait for button press
    while share_button_flag.get() != 1:
        yield 0
    
    # write commands to UART2
    last_cmd_type = 0
    cmd_type = share_cmd_type.get()
    while(cmd_type != TYPE_CMDS_DONE):
        
        # get command type
        cmd_type = share_cmd_type.get()

        # write type str ("PU" or "PD") if it has changed
        if cmd_type != last_cmd_type:
            if cmd_type == TYPE_PEN_UP:
                uart.write("PU\r\n")
            elif cmd_type == TYPE_PEN_DOWN:
                uart.write("PD\r\n")
        elif cmd_type > 0:
            # write each coordinate pair ("theta0, theta1")
            uart.write("%d, %d\r\n" % (share_theta0.get(), share_theta1.get()))
        
        last_cmd_type = cmd_type
        yield 0
    
    # write "END"
    uart.write("END\r\n")

    # indicate all tasks have finished
    share_cmd_type.put(TYPE_COMMS_DONE)
    yield 0
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

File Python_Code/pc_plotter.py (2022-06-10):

'''@file        pc_plotter.py
   @brief       This file contains a function for plotting the arm position and drawn
                shapes live on a PC to match the physical plotter.
   @author      Ryan Ghosh
   @copyright   This file is licensed under the CC BY-NC-SA 4.0
                Please visit https://creativecommons.org/licenses/by-nc-sa/4.0/
                for terms and conditions of the license.
   @date        June 10, 2022
'''

import serial
import math
import matplotlib
from matplotlib import pyplot as plt
import numpy as np
import imageio

# constants for converting theta to coordinates
W = 270
H = 90
D = 42
RD = 40

# constants for converting microsteps to radians
STEPS_PER_ROTATION  = 200
MICROSTEPS = 8
MS_PER_RADIAN = 1 / (2 * math.pi) * STEPS_PER_ROTATION * MICROSTEPS

# constants for converting microsteps to account for homing angle and motor direction
STEPS_PER_ROTATION  = 200
MOTOR1_HOMING_ANGLE = -int(68.27 / 360 * STEPS_PER_ROTATION * MICROSTEPS * 6)
MOTOR1_POLARITY     = 1
MOTOR2_HOMING_ANGLE = -int((34.7/2 + 60.24 + 0.9) / 40 * STEPS_PER_ROTATION * MICROSTEPS)
MOTOR2_POLARITY     = -1

def revert_motor1_target(microsteps):
    ''' @brief      Converts the motor1 target value for plotting.
        @details    Takes in a target value for motor1 that was sent to
                    the TMC4210 and converts it for plotting, undoing
                    modifications that were made based on the direction
                    of the motor and its angle when the limit switch is triggered.
        @param      Target position in microsteps sent to the TMC4210.
        @return     Target position for motor1 in microsteps for plotting.
    '''

    # revert target position sent to the TMC4210 to 
    # undo homing angle and motor direction modifications
    return microsteps / MOTOR1_POLARITY + MOTOR1_HOMING_ANGLE

def revert_motor2_target(microsteps):
    ''' @brief      Converts the motor2 target value for plotting.
        @details    Takes in a target value for motor2 that was sent to
                    the TMC4210 and converts it for plotting, undoing
                    modifications that were made based on the direction
                    of the motor and its angle when the limit switch is triggered.
        @param      Target position in microsteps sent to the TMC4210.
        @return     Target position for motor2 in microsteps for plotting.
    '''

    # revert target position sent to the TMC4210 to 
    # undo homing angle and motor direction modifications
    return microsteps / MOTOR2_POLARITY + MOTOR2_HOMING_ANGLE

if __name__ == '__main__':

    # variables for plotting
    ## Whether or not the pen is currently down
    pen_down = False

    ## 2D list for the position of the points on the robot
    robot = [[0 for _ in range(3)] for _ in range(2)]   # [x or y][pt idx]

    ## List of lists of (x,y) tuples, with 1 outer list for each shape
    shapes = []

    ## Index of the current shape being drawn
    curr_shape = -1

    # create figure
    plt.ion()
    fig = plt.figure()
    
    # receive data from nucleo
    with serial.Serial('COM4', 115200) as ser:
        ser.flush()
        
        # read data
        i = -1
        started = False
        while(True):

            # read line
            line = ser.readline().decode().strip('\r\n')

            # if end of data
            if line == "END":
                break
            
            # elif new command
            elif line == "PU" or line == "PD":
                started = True
                i += 1

                # pen up
                if line == "PU":
                    pen_down = False
                
                # pen down
                else:

                    # start a new shape if the pen is not down already
                    if not pen_down:
                        curr_shape += 1
                        shapes.append([])
                    pen_down = True
            
            # elif a coordinate pair was sent
            elif started:

                # read theta0 and theta1 from line
                line = line.split(',')
                theta0 = float(line[0])
                theta1 = float(line[1])

                # convert microsteps to radians
                theta0 = revert_motor1_target(theta0) / MS_PER_RADIAN
                theta1 = revert_motor2_target(theta1) / MS_PER_RADIAN

                # robot - point 0 (pivot point)
                robot[0][0] = W
                robot[1][0] = H

                # robot - point 1 (cart position on linear rail)
                alpha = 1/6 * theta0
                arm_radius = -RD * theta1 / (2 * math.pi)
                robot[0][1] = robot[0][0] - arm_radius * math.cos(alpha)
                robot[1][1] = robot[1][0] - arm_radius * math.sin(alpha)

                # robot - point 2 (pen position)
                robot[0][2] = robot[0][1] + D * math.sin(alpha)
                robot[1][2] = robot[1][1] - D * math.cos(alpha)

                # add pen position to current shape if pen down
                if pen_down:
                    shapes[curr_shape].append((robot[0][2], robot[1][2]))

                # clear plot
                plt.clf()

                # plot robot
                plt.plot(robot[0], robot[1])

                # plot all shapes up to and including curr_shape
                for i in range(curr_shape + 1):
                    x_list = []
                    y_list = []
                    for pt in shapes[i]:
                        x_list.append(pt[0])
                        y_list.append(pt[1])
                    plt.plot(x_list, y_list)

                # format plot
                plt.xlabel('x (mm)')
                plt.ylabel('y (mm)')
                axes = plt.gca()
                axes.set_aspect(1)
                plt.xlim(-50, 300)
                plt.ylim(-50, 200)

                # redraw plot
                fig.canvas.draw()
                fig.canvas.flush_events()

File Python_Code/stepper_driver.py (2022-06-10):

'''@file        stepper_driver.py
   @brief       This file contains a stepper driver class for controlling a TMC4210 and TMC2208.
   @author      Ryan Ghosh
   @copyright   This file is licensed under the CC BY-NC-SA 4.0
                Please visit https://creativecommons.org/licenses/by-nc-sa/4.0/
                for terms and conditions of the license.
   @date        June 10, 2022
'''

import pyb

class Stepper_Driver:
    ''' @brief      A stepper driver class for controlling a TMC4210 and TMC2208.
        @details    Objects of this class can be used to interface with a TMC4210
                    and TMC2208 in order to control a stepper motor.
    '''

    def __init__(self, spi, en, cs, 
                 x_max, v_min, v_max, pulse_div, ramp_div, 
                 a_max, pmul, pdiv):
        ''' @brief              Constructor for Stepper_Driver.
            @details            Sets registers in a TMC4210 with values passed in
                                and enables the step/dir interface.
            @param spi          SPI pin.
            @param en           TMC2208 enable pin.
            @param cs           Chip select pin.
            @param x_max        Max position the stepper can move to, in microsteps.
            @param v_min        V_MIN register value.
            @param v_max        V_MAX register value.
            @param pulse_div    PULSE_DIV register value.
            @param ramp_div     RAMP_DIV register value.
            @param a_max        A_MAX register value.
            @param pmul         PMUL register value.
            @param pdiv         PDIV register value.
        '''

        # set SPI and Pin objects to those passed in
        ## SPI pin
        self.spi = spi      # mode=SPI.CONTROLLER
        
        ## TMC2208 enable pin
        self.en = en        # mode=Pin.OUT_PP
        
        ## Chip select pin
        self.cs = cs        # mode=Pin.OUT_PP

        # set max position
        ## Max position the stepper can move to, in microsteps
        self.x_max = x_max
        
        # enable step/dir interface
        self.enable_step_dir()

        # set initial V_MIN and V_MAX
        self.set_velocity(v_min, v_max)

        # set PULSE_DIV and RAMP_DIV
        self.set_pulse_div(pulse_div)
        self.set_ramp_div(ramp_div)

        # set A_MAX, PMUL, and PDIV
        self.set_acceleration(a_max)
        self.set_pmul(pmul)
        self.set_pdiv(pdiv)

        # set R_M to 00 (ramp_mode)
        self.set_ramp_mode()

    def send_recv(self, send, recv=None):
        ''' @brief          Sends and receives data to and from the TMC4210.
            @details        Sets the chip select pin and uses spi.send_recv
                            to send and receive data to and from the TMC4210
                            via SPI.
            @param send     Datagram to send to the TMC4210.
            @param recv     Datagram in which to store the received datagram.
            @return         Bytes received from the TMC4210.
        '''

        self.cs.low()
        if recv is None:
            recv = self.spi.send_recv(send)
        else:
            self.spi.send_recv(send, recv)
        self.cs.high()

        # # debugging
        # print('\nsend:')
        # self.print_arr(send)
        # send[0] |= 0b00000001
        # self.cs.low()
        # recv_temp = self.spi.send_recv(send)
        # self.cs.high()
        # print('\nrecv:')
        # self.print_arr(recv_temp)

        return recv

    def enable_step_dir(self):
        ''' @brief      Enables the step/dir interface of the TMC4210.
            @details    Sets the en_sd bit to 1 to enable the step/dir interface.
        '''

        # set en_sd bit to 1 and reference switches to normally closed:
        send = bytearray([0b01101000,
                          0b00000000,
                          0b00000000,
                          0b00100001])
        self.send_recv(send)

    def set_ramp_mode(self, mode='ramp_mode'):
        ''' @brief          Sets RAMP_MODE.
            @details        Sets the RAMP_MODE register value to 00 for ramp_mode
                            or 10 for velocity_mode.
            @param mode     Mode to set.
        '''

        send = bytearray([0b00010100,
                          0b00000000,
                          0b00000000,
                          0b00000000])
        if mode == 'velocity_mode':
            send[3] = 0b00000010
        self.send_recv(send)

    def enable(self):
        ''' @brief      Enables the TMC2208.
            @details    Sets the en pin low to enable the TMC2208.
        '''

        # set EN pin on the TMC2208
        self.en.low()

    def disable(self):
        ''' @brief      Disables the TMC2208.
            @details    Sets the en pin high to disable the TMC2208.
        '''

        # set EN pin on the TMC2208
        self.en.high()

    def set_pulse_div(self, pulse_div):
        ''' @brief              Sets PULSE_DIV.
            @details            Sets the PULSE_DIV register value to what is passed in.
            @param pulse_div    PULSE_DIV value to set.
        '''

        # (pulse_div should be a 4-bit unsigned int)

        send = bytearray([0b00011001,
                          0b00000000,
                          0b00000000,
                          0b00000000])
        recv = bytearray(4)
        self.send_recv(send, recv)
        recv[2] &= 0x0F
        recv[2] |= (pulse_div << 4)
        recv[0] = send[0] & 0b11111110
        self.send_recv(recv)

    def set_ramp_div(self, ramp_div):
        ''' @brief              Sets RAMP_DIV.
            @details            Sets the RAMP_DIV register value to what is passed in.
            @param ramp_div     RAMP_DIV value to set.
        '''

        # (ramp_div should be a 4-bit unsigned int)

        send = bytearray([0b00011001,
                          0b00000000,
                          0b00000000,
                          0b00000000])
        recv = bytearray(4)
        self.send_recv(send, recv)
        recv[2] &= 0xF0
        recv[2] |= ramp_div
        recv[0] = send[0] & 0b11111110
        self.send_recv(recv)

    def set_pmul(self, pmul):
        ''' @brief          Sets PMUL.
            @details        Sets the PMUL register value to what is passed in.
            @param pmul     Value of PMUL to set.
        '''

        # (pmul should be a 7-bit unsigned int)

        send = bytearray([0b00010011,
                          0b00000000,
                          0b00000000,
                          0b00000000])
        recv = bytearray(4)
        self.send_recv(send, recv)
        recv[2] &= 0b10000000
        recv[2] |= pmul
        recv[0] = send[0] & 0b11111110
        self.send_recv(recv)

    def set_pdiv(self, pdiv):
        ''' @brief          Sets PDIV.
            @details        Sets the PDIV register value to what is passed in.
            @param pdiv     Value of PDIV to set.
        '''
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

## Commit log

2022-05-17 Add printed mounts for attaching to the leftmost holes in the base plate
    [Plate Mount^Plotter Main Assembly.STL, Toolhead.SLDASM]
2022-06-10 Add python code and hpgl files
    [BASE-PLATE-2.DXF, Clipboard Clamp.STL, MGN12 1515 Rail Installation Guide.SLDPRT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]
2022-06-10 Rename stls
    [3mm_shaft_retainer_x2_rev1.STL, Printed M5 Washer.STL, cable_anchor_x1_rev1.STL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]
2022-06-11 Add square nuts and feet to cad model, start on readme
    [Toolhead.SLDASM]
2022-06-11 Finish kinematics and BOM sections
2022-06-11 Add task diagram, remove extra comment, add missing newline to documentation website
    [tasks.py]
